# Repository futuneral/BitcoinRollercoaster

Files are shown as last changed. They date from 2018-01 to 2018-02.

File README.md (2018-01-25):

# Bitcoin Rollercoaster Guy

This is the complete set of assets/sources to make your own Bitcoin Rollercoaster Guy desk toy. It is based on the awesome 3D model by rgremill (https://www.thingiverse.com/thing:2523635). I addded a stand, servo and some electronics to make it read current BTC price and position the cart accordingly.

Please follow the guidelines below to build and setup the toy. Have fun on the Bitcoin rollercoaster!

Any donations to this address will be much appreciated: <b>1LAJ6Aa1gvv5B4MRmAoizPNHKHsTvC9iGt</b>

## Parts

1. 1x D1 Mini NodeMCU ESP8266 ESP-12 module (I got one from eBay, and I believe it's a clone of https://wiki.wemos.cc/products:d1:d1_mini)
2. DIYmall 0.96" Yellow& Blue 128X64 OLED display (http://www.diymalls.com/OLED/0.96-blue-and-yellow-oled-display)
3. SG90 9g servo (TP-SG90)
4. Some small screws
5. Access to 3D printer or 3D printing service

## How to print

Download .stl files from the models folder. Most of the cart parts a printed as they are in rgremill's project (so technically you can download from there). Only the wheel platform is modified to accept the servo. Note you may need to print with supports and/or post process the part.
The top of the base is best printed upside down and it should not require supports.

Once printed, you may want to test that the halves of the horizontal bar between the stands can more or less easily be connected together. You may need file one of them a bit. Also try plugging the stands into the base and see if they fit. Some filing may be needed here too.

For the parts that I designed, I provided Autodesk Fusion 360 (free) source files. Feel free to modify them if you need to adjust for the actual hardware you have.

## Electronics

I'm gonna have to come back and maybe add a diagram, but here are the connections than need to be made on the MCU/screen/servo

ESP8266 D1 -> OLED SCL

ESP8266 D2 -> OLED SDA

ESP8266 3.3v -> OLED VCC

ESP8266 GND -> OLED GND

ESP8266 5v -> Servo +

ESP8266 GND -> Servo GND

ESP8266 D7 -> Servo Signal

## Software

The MCU we're working with is very nice in that it has onboard USB, so you can reprogram it later without disassembling the base. Just follow https://wiki.wemos.cc/tutorials:get_started:get_started_in_arduino#using_boards_manager to set up your Arduino environment with NodeMCU and then load the code from the src folder. 

The code is using some libraries you can download from their respective websites, or from the included archive.

The most magic is coming from WiFi manager (https://github.com/tzapu/WiFiManager). This awesome library allows for user friendly wi-fi setup on MCU without even needing a screen or buttons. 

The rest are standard Adafruit GFX, Servo, ArduinoJson as well as standard ESP8266 libraries.

I included two classes for network implementation. One works with Coinbase API and the other one is for Coindesk. Feel free to add your own. As long as they have the same API you won't need to change the main code.

Please also find `config.h` where you can provide some configuration items for the toy. One of them worth mentioning is `MECHANICAL_OFFSET`. Remember when I said the platform doesn't need to be exacly level at zero? This is the value that will help you correct that. Experiment and set positive or negative offset in degrees until the cart is level.

## How to assemble

The assembly should be pretty straightforward if a bit awkward. The trickiest part is probably routing the cable from servo into the base.

This is the method I found to be the easiest. It's better to install the servo into the platform first. One of the stands has a channel inside it. You will have to cut off the connector from the servo, make sure you cut close to the connector, so you have enough length. Now route the cable through the "ring" in the platform (going from inside out). Tie a piece of fishing line to the wire and route it through the channel in the stand (from top end to bottom). By carefully pulling on the fishing line, route the wire through the stand's channel.

The other stand has the slot for servo's arm. You can either glue the arm inside the slot or use some heated thin wire to pin it down. You can also just put it there as is, you'll use a screw to tie it down later. This however may result in a bit of play.

Before fully assembling the top part, you'll need to solder the servo wire onto the board (see if you want to route the cable into the base at this step, or you're ok resoldering it later), and (with all code loaded) turn the ESP8266 on. The first instruction in the script is to "zero" the platform. This will move the servo into intial position, you can turn the board off now. 

Now some coordinated actions will be needed. Hold the platform level and the non-hollow stand vertically. Plug servo's shaft into the arm's socket. Don't worry about being a couple degrees off. Now put in a screw and tighten. Don't let go of the assembly. Take the other stand and plug its horizontal into its counterpart on the first stand. You may also need to pull on the wire to remove any slack to let the top "bearing" on the stand to get into the "ring" on the platform. If your wire is not routed into the base yet, do it now. You can now plug the stands into the base. You can glue them in with acetone if your parts are from ABS. alternatively, use some plastic-friendly glue.

The OLED panel should fit behind its window, and you'll need something to lock its bottom part there. I used pieces of filament that I melted with soldering iron.

The bottom of the base should snap into place and you can secure it with a screw in the middle.

I would recommend attaching the card only after these steps and after confirming that the toy works as expected. Simply glue it on top of the platform. Note: the axis of the servo is not perfectly in the middle of the platform. Make sure Bitcoin Guy sits on the short side of the platform, this helps with balance.

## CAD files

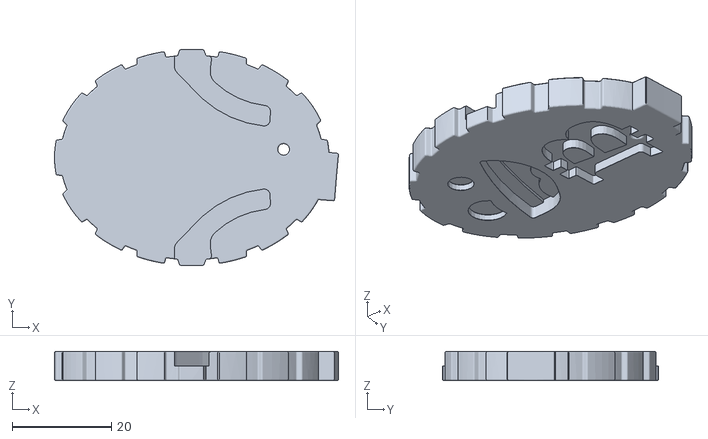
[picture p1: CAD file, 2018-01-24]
models/ASM_BitCoin_STL.stl
57.3 x 43.7 x 5.90

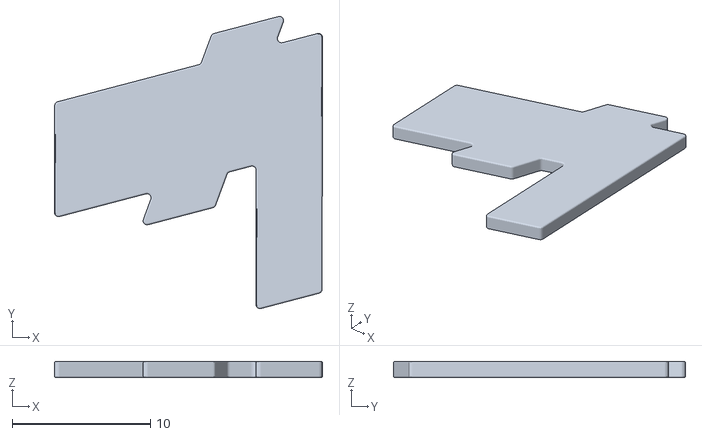
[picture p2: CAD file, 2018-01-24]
models/ASM_Lsymbol_STL.stl
19.4 x 21.2 x 1.18

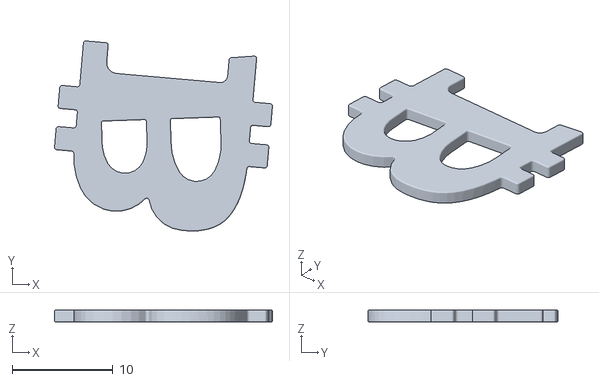
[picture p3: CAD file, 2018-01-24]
models/ASM_Bsymbol_STL.stl
21.6 x 18.8 x 1.18

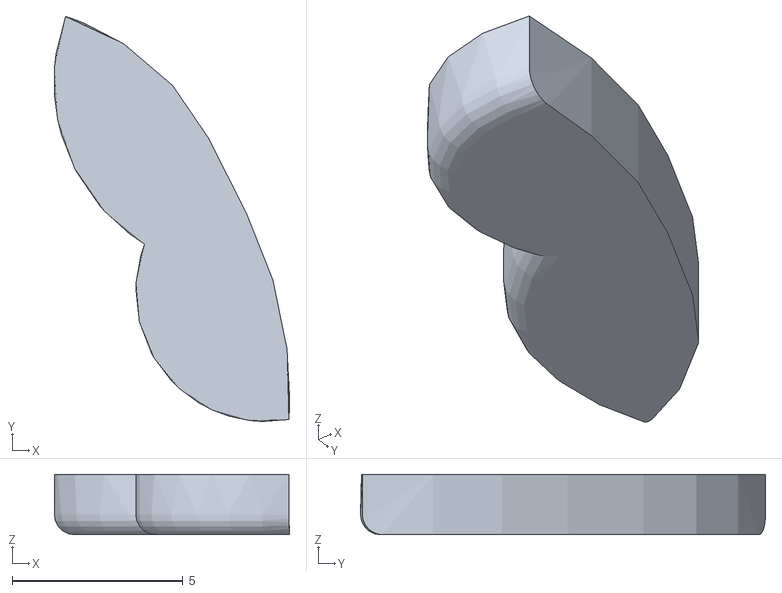
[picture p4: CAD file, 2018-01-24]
models/ASM_Tongue_STL.stl
6.89 x 11.9 x 1.77

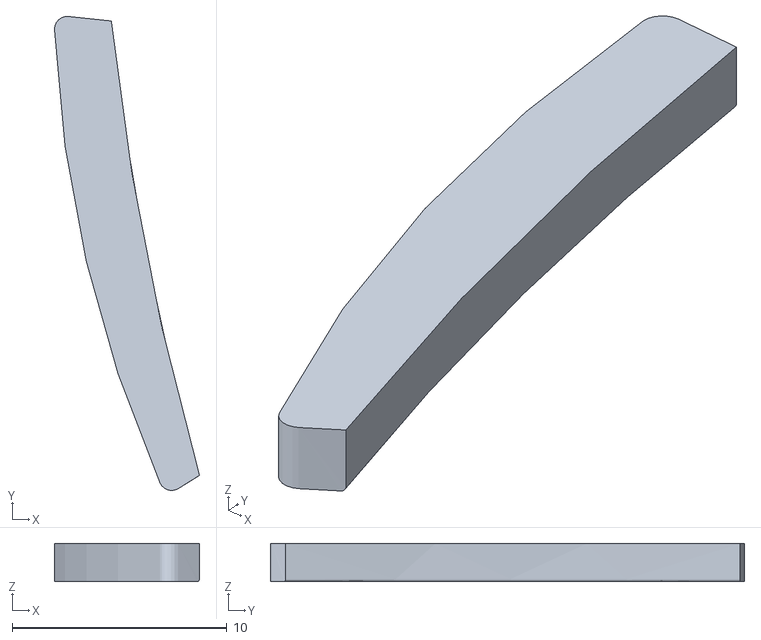
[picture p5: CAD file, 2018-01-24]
models/ASM_Teeth_STL.stl
6.75 x 22.1 x 1.77

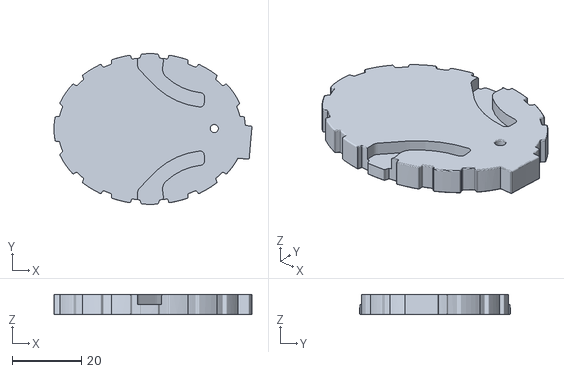
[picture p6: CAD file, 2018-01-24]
models/ASM_LiteCoin_STL.stl
57.3 x 43.7 x 5.90

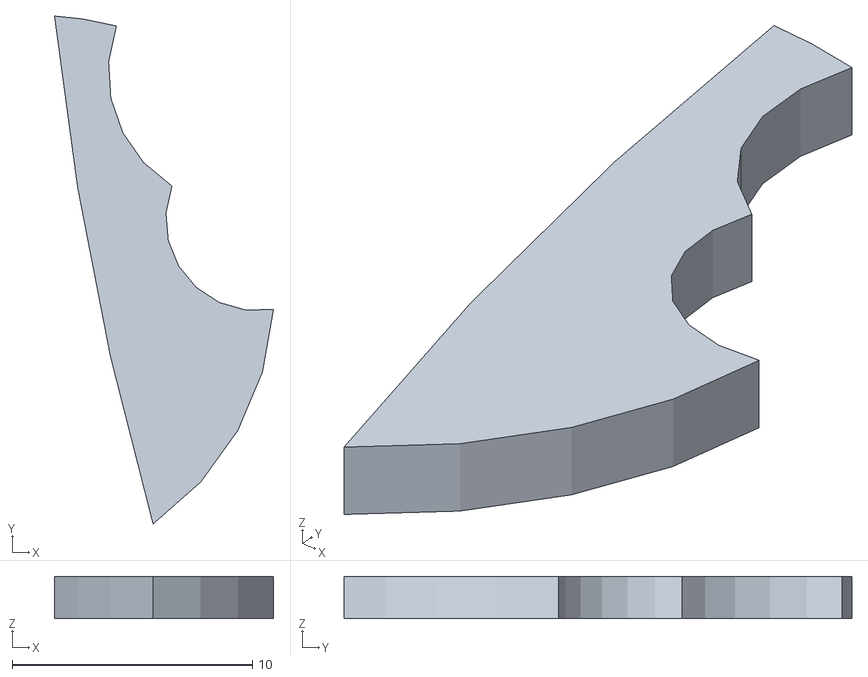
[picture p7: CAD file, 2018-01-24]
models/ASM_Mouth_STL.stl
9.12 x 21.2 x 1.77

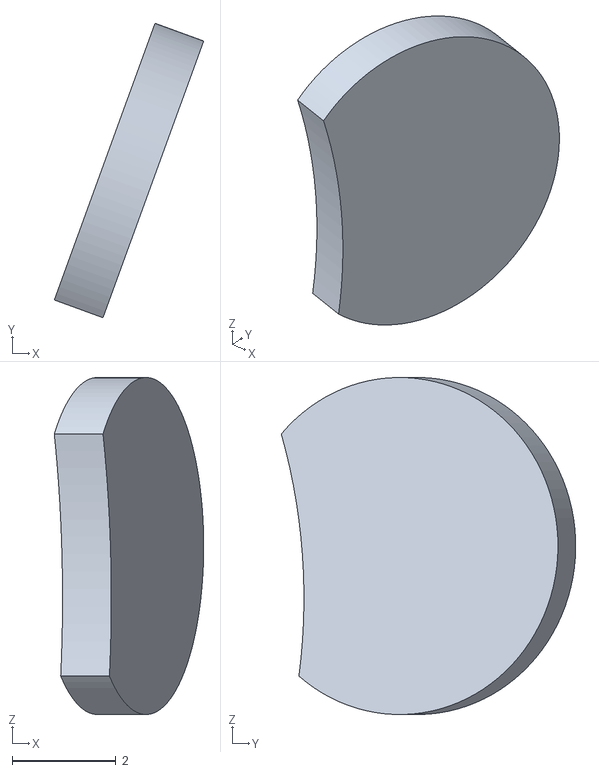
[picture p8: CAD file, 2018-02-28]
models/p3_eye_left.stl
2.88 x 5.68 x 6.50

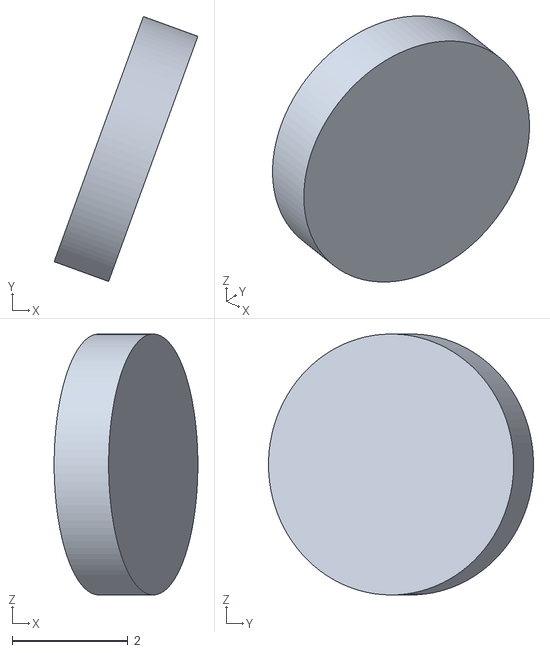
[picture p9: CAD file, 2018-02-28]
models/p3_eye_right.stl
2.48 x 4.57 x 4.50

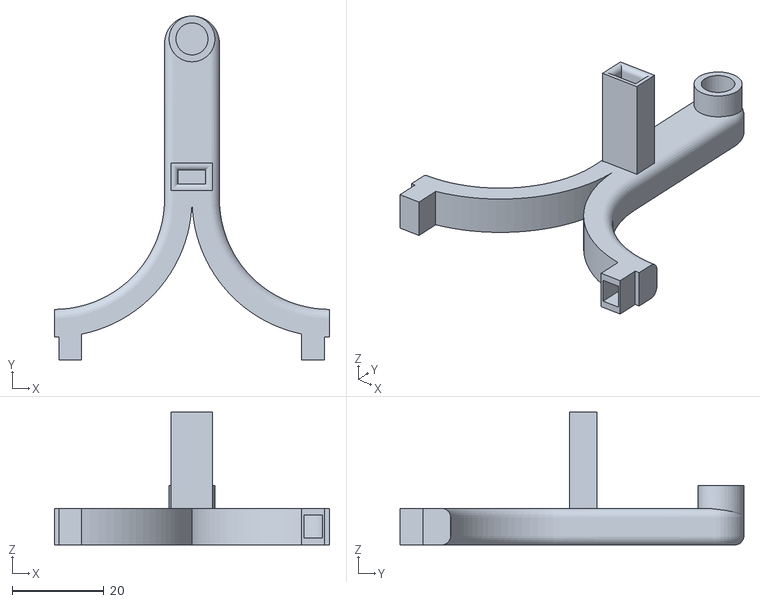
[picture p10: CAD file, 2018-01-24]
models/stand_front.stl
60.0 x 75.1 x 29.0

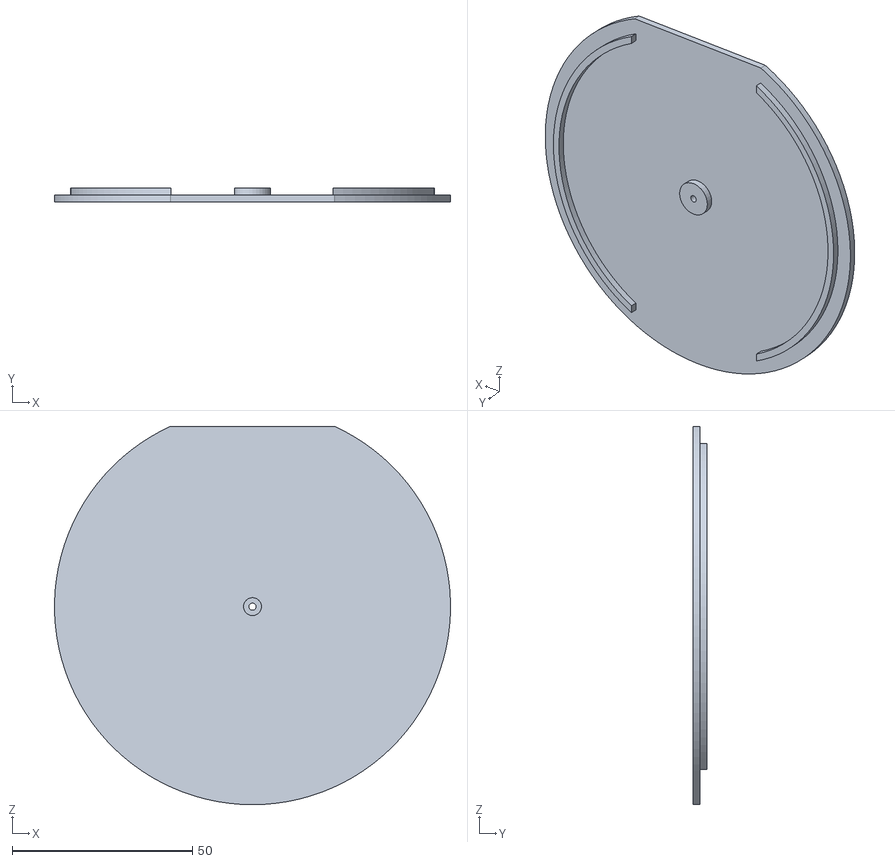
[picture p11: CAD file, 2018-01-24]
models/base_bottom.stl
110.0 x 4.00 x 105.1

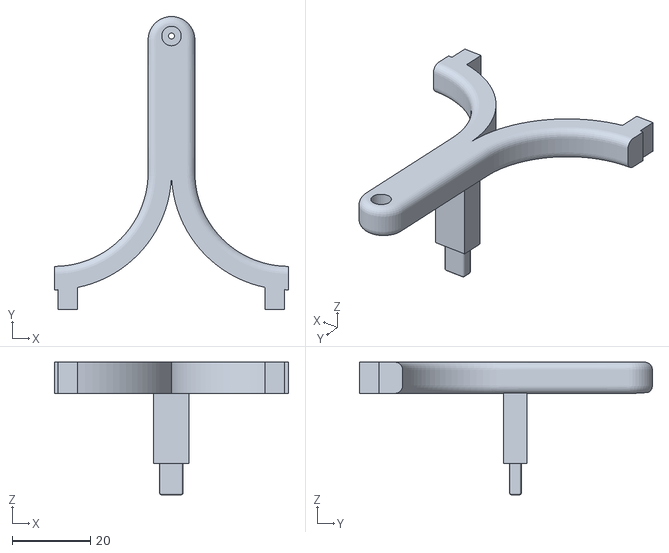
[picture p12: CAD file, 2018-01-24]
models/stand_back.stl
60.0 x 75.0 x 34.0

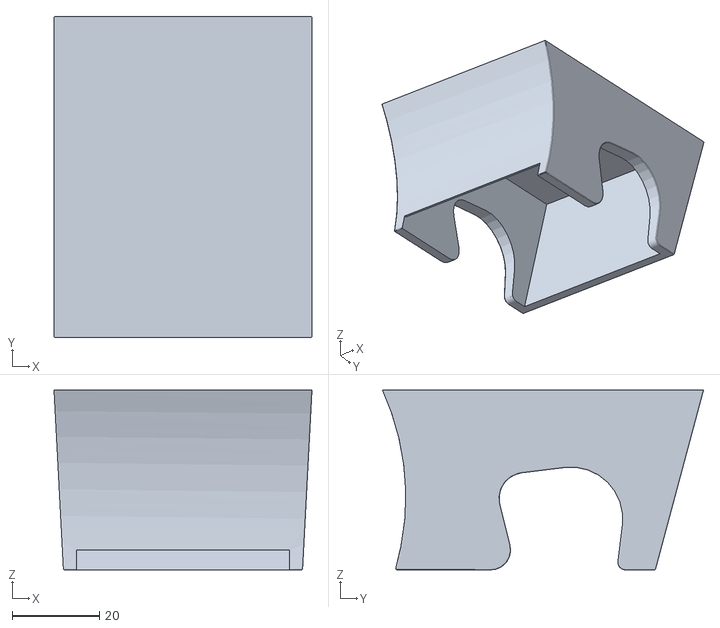
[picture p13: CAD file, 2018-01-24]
models/CART_TOP_STL.stl
59.2 x 73.7 x 41.3

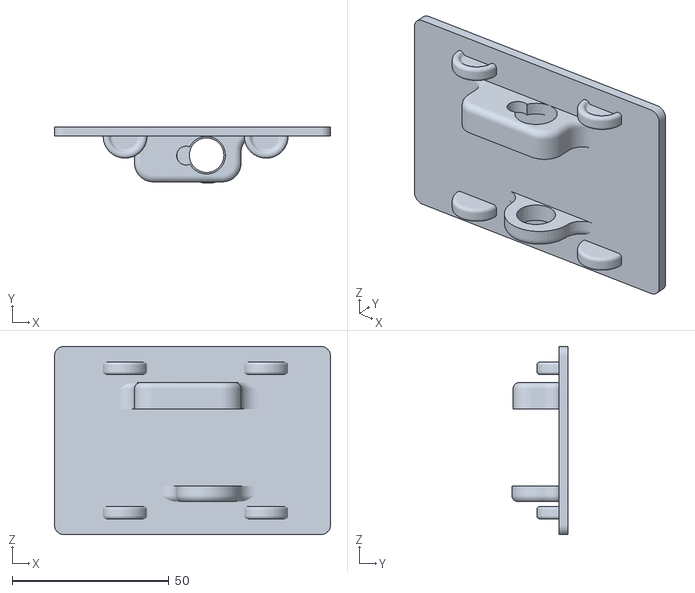
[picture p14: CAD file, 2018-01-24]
models/platform.stl
88.0 x 18.0 x 60.0

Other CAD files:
models/RIGHT_HAND_v2_STL.stl
models/CART_SEAT_STL.stl
models/LEFT_HAND_v6_STL.stl
models/base_top.stl
models/f3d/base_bottom.f3d
models/f3d/base_top.f3d
models/f3d/platform.f3d
models/f3d/stand_back.f3d
models/f3d/stand_front.f3d

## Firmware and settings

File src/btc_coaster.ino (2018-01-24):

 #define min(a,b) ((a)<(b)?(a):(b))

#include "config.h"
#include "btc_network.h"
#include "btc_coinbase.h"
#include "btc_graph.h"
#include "ESP8266WiFi.h"
#include <DNSServer.h>            //Local DNS Server used for redirecting all requests to the configuration portal
#include <ESP8266WebServer.h>     //Local WebServer used to serve the configuration portal
#include <WiFiManager.h>          //https://github.com/tzapu/WiFiManager WiFi Configuration Magic
#include <Servo.h>


float history[HISTORY_SIZE];
WiFiClient client;
float lastRate = 0;
float lastAngle = 0;
Servo cart;
//Btc_Coindesk net;
Btc_Coinbase net;
Btc_Graph graph;
Adafruit_SSD1306 display(-1);
int demoCount = 0;


void setup() {
  Serial.begin(115200);
  Serial.print("Start: ");
  graph.begin();
  cart.attach(CART_PIN);
  rotateCart((int)MAX_ANGLE);

  if(!DEMO_MODE){
    WiFiManager wifiManager;
    wifiManager.autoConnect("BtcGuy");
    Serial.println(WiFi.localIP());
    graph.connected();
    net.connect();
  }
}

void loop() {
  process();
}

void process(){
  if(DEMO_MODE){
        float rate = 4000.0f + 100.0f * sin((float)demoCount/3 )  ;
  
        push(rate);
        graph.drawScreen();
        positionCart();
        demoCount++;

        delay(2000);
    
  }else{
    if(net.connected()){
      float rate = net.readRate();
      if(rate >= 0){
        push(rate);
        graph.drawScreen();
        positionCart();
      }
    }
  }
}

void positionCart(){
  cart.attach(13);
  float rate = history[0];
  float lastRate = history[HISTORY_SIZE - 1];

  float delta = 100 * ((rate - lastRate) / lastRate);
  Serial.print("Rate: ");
  Serial.println(rate);
  Serial.print("lastRate: ");
  Serial.println(lastRate);
  Serial.print("Delta: ");
  Serial.println(delta);
  
  float angle = delta * DEGREE_PER_PERCENT;
  if(angle > MAX_ANGLE){
    angle = MAX_ANGLE;
  }else if(angle < -MAX_ANGLE){
    angle = -MAX_ANGLE;
  }
  angle = angle + MAX_ANGLE;

  interpolateAngle(lastAngle, angle);
  
  lastAngle = angle;
  delay(1000);
  cart.detach();
}

void rotateCart(int angle){
  cart.write(angle + MECHANICAL_OFFSET);
}

void interpolateAngle(float start, float finish){
  int count = (int)abs(finish - start);
  float currentAngle = start;
  float angleStep = finish > start ? 1.0f : -1.0f;
  for(int i=0;i<count;i++){
    rotateCart((int)currentAngle);
    currentAngle += angleStep;
    delay((int)(1000.0f / SPEED_DEG_PER_S));
  }
}


void push(float rate){
  if(history[0] == 0){
    for(int i=0;i<HISTORY_SIZE;i++){
      history[i] = rate;
    }
  }

  for(int i=HISTORY_SIZE-1; i>0;i--){
    history[i] = history[i-1];
  }
  history[0] = rate;
}

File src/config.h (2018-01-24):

#ifndef _BTC_COASTER_CONFIG_H
#define _BTC_COASTER_CONFIG_H

// Number of data points on the graph
#define HISTORY_SIZE 20
// Graph width in pixels
#define GRAPH_WIDTH 150
// Graph height in pixels
#define GRAPH_HEIGHT 80
// Max cart rotation angle
#define MAX_ANGLE 60.0f
// Number of degrees to turn when price changes by 1% over the length of the graph
#define DEGREE_PER_PERCENT 30.0f
// Value (in degrees) for correcting mechanical imperfections (i.e. when card is not level in the mid position)
#define MECHANICAL_OFFSET 0
// Time between refreshes
#define REFRESH_DELAY 300000

#define GRAPH_WIDTH 128
#define GRAPH_HEIGHT 20

// Screen width in pixels
#define SCREEN_WIDTH 128
// Screen height in pixels
#define SCREEN_HEIGHT 63

#define SPEED_DEG_PER_S 20.0f
#define CART_PIN 13

#define DEMO_MODE false


#endif
